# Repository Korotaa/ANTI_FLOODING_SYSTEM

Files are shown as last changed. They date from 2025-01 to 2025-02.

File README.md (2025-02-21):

# Système anti inondation
[https://github.com/Korotaa/ANTI_FLOODING_SYSTEM](https://github.com/Korotaa/ANTI_FLOODING_SYSTEM)
## I. Besoins du système  
1. Détection proactive des niveaux d’eau à l’aide de capteurs robustes.
2. Actionnement automatisé pour évacuation d’eau via une pompe submersible.
3. Signalisation locale et/ou à distance en cas de risque.
4. Résilience énergétique grâce à une batterie de secours.
## II. Design contraintes
1. Fiabilité : Utilisation de capteurs et d’actionneurs éprouvés.
2. Accessibilité : Matériel standard et technologies abordables.
3. Évolutivité : Possibilité d’intégrer des fonctionnalités avancées comme la communication IoT.
##  III. Architecture
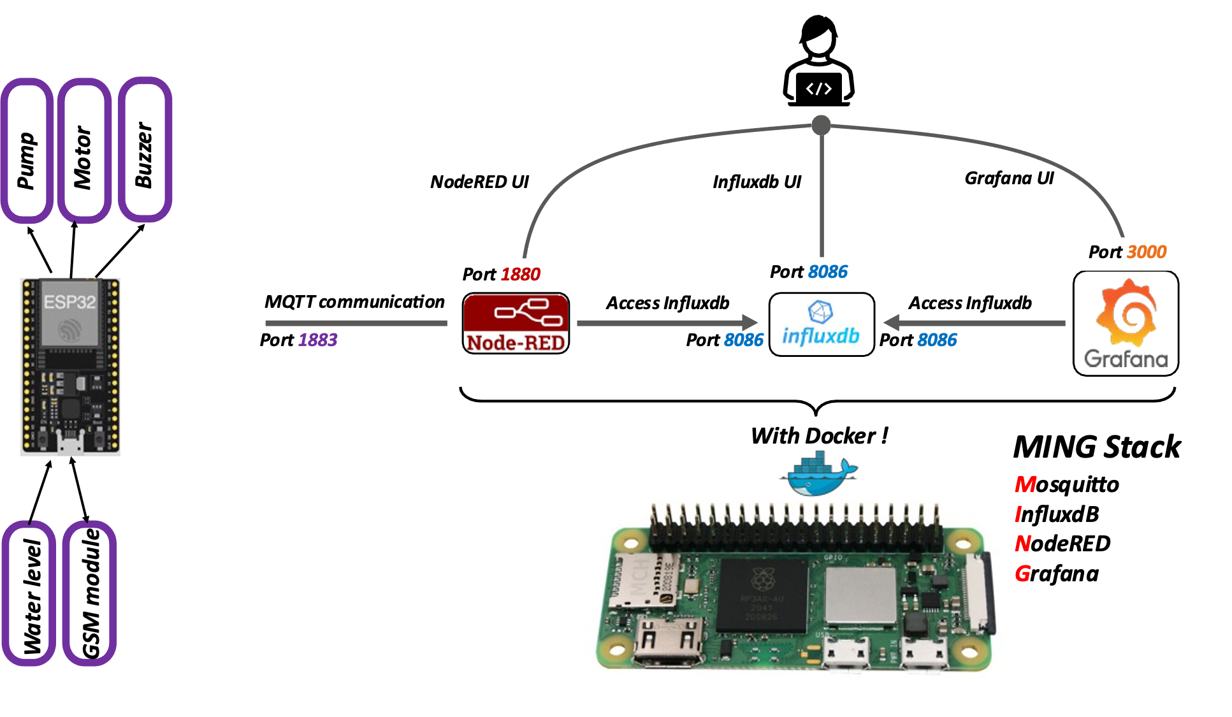
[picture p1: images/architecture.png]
Architecture

## IV. schéma électronique du End-device
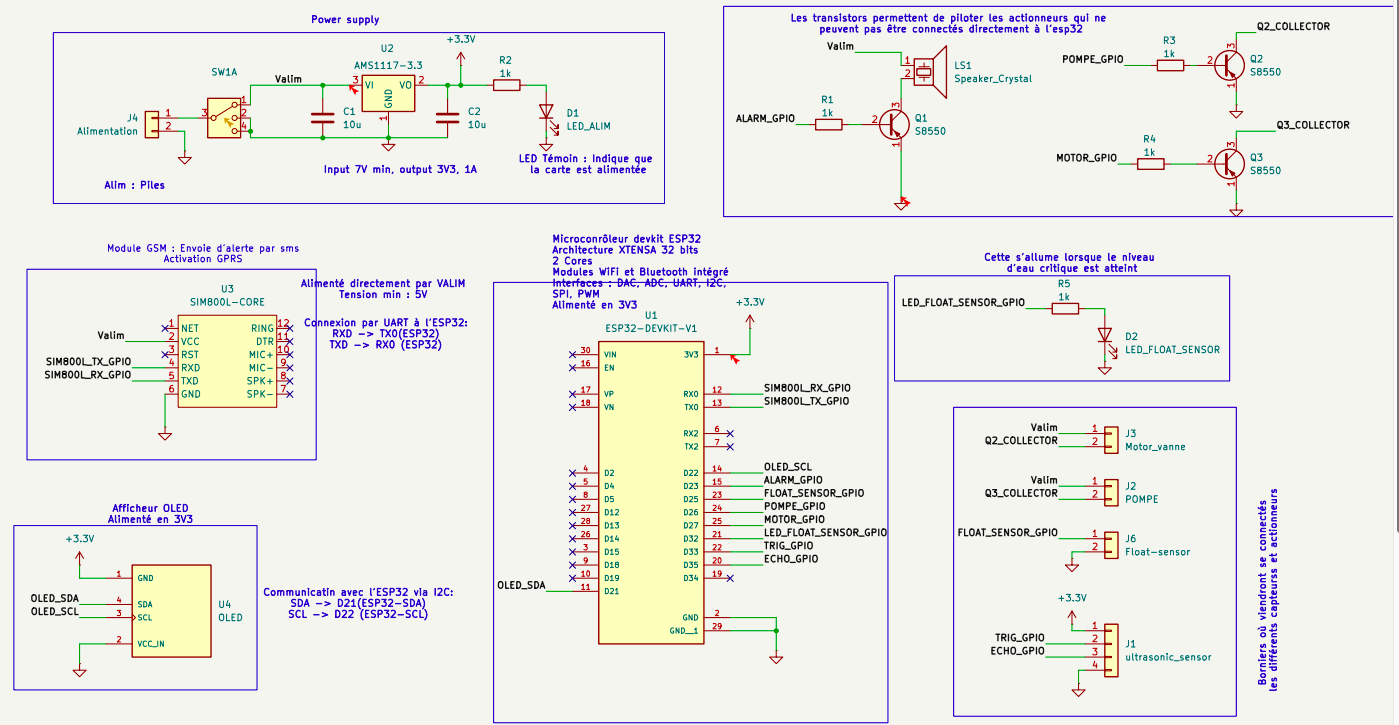
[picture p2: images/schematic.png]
Schematic

## V. PCB
**NB : Le pcb est conçu pour faciliter le prototypage sur PCB double face perforé**
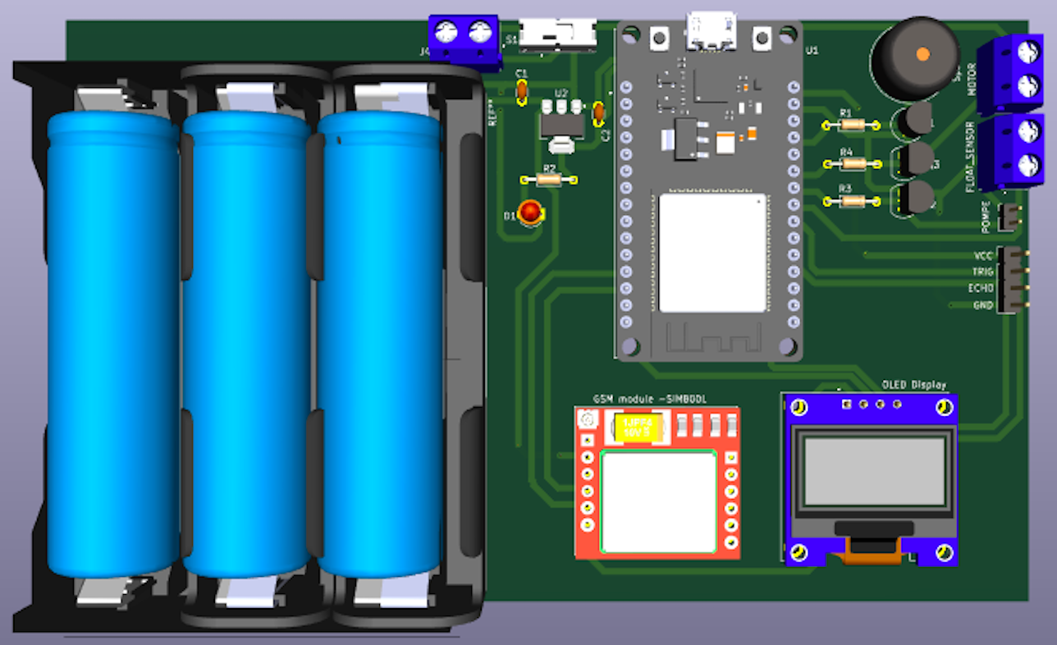
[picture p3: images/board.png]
PCB board


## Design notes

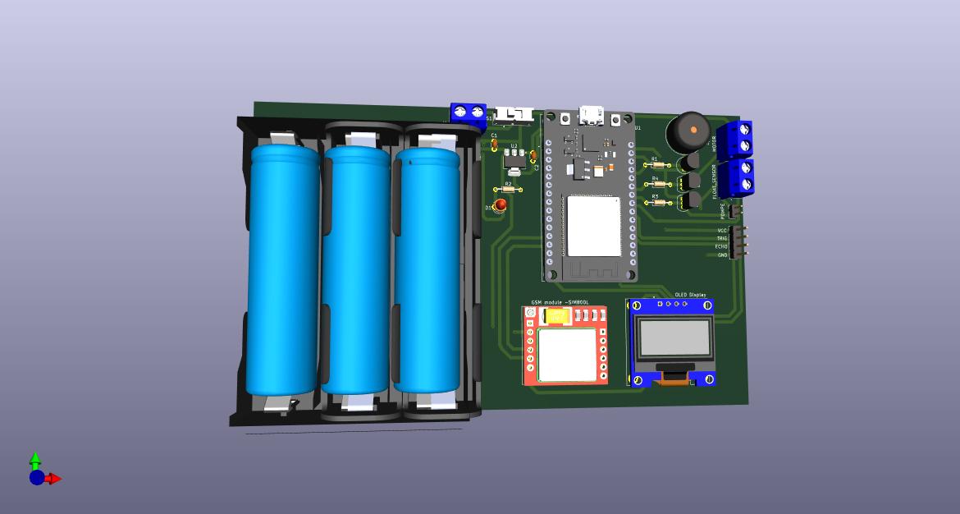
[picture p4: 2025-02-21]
Hardware/anti-innondation-board/Anti_innondation_project1.jpg

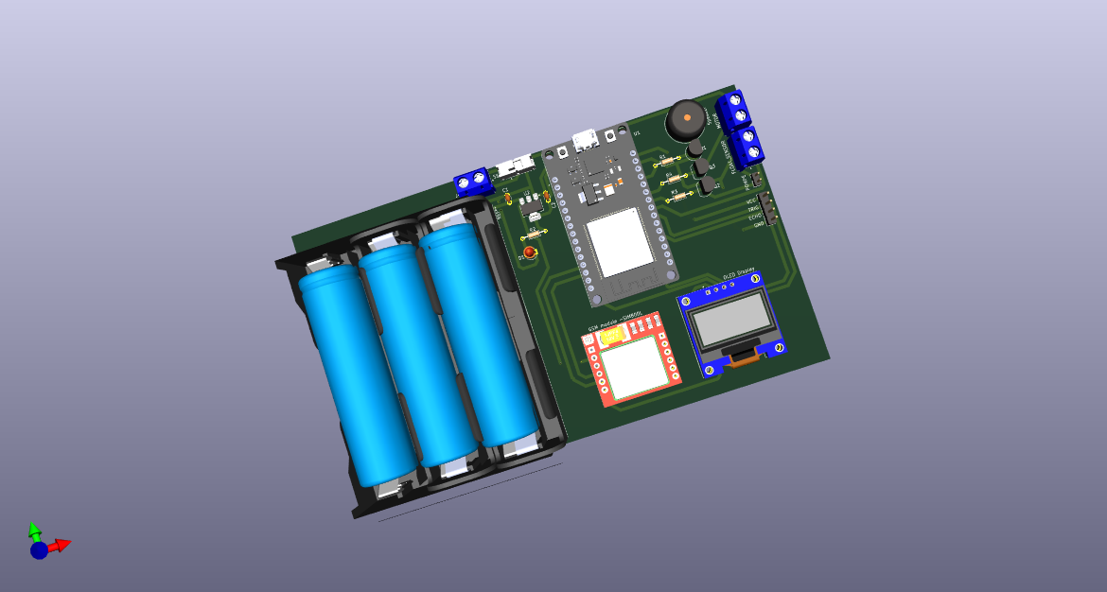
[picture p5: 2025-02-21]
Hardware/anti-innondation-board/pcb_img.png

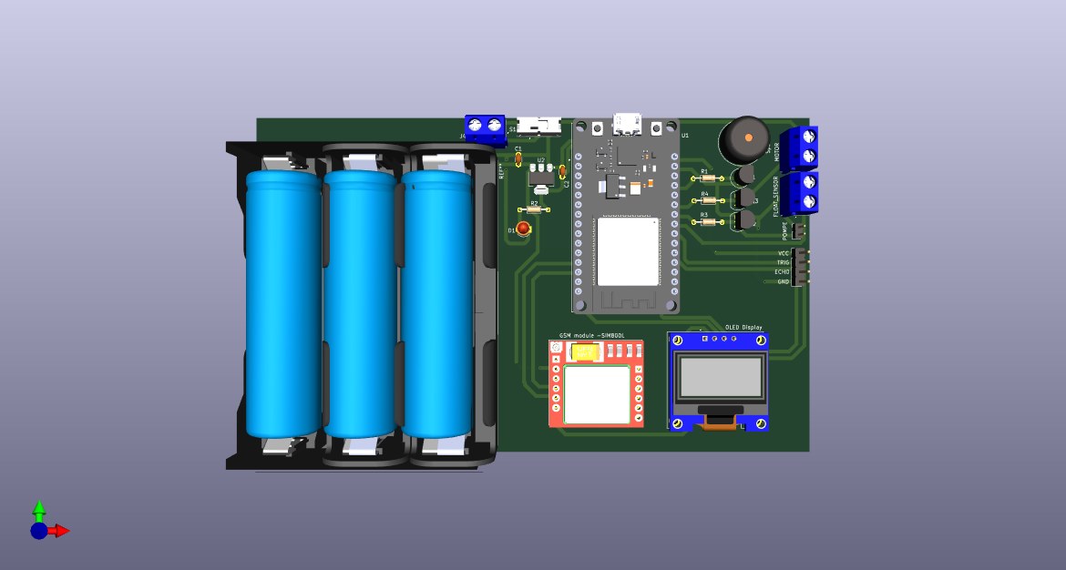
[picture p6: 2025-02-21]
Hardware/anti-innondation-board/anti-innondation-board.png

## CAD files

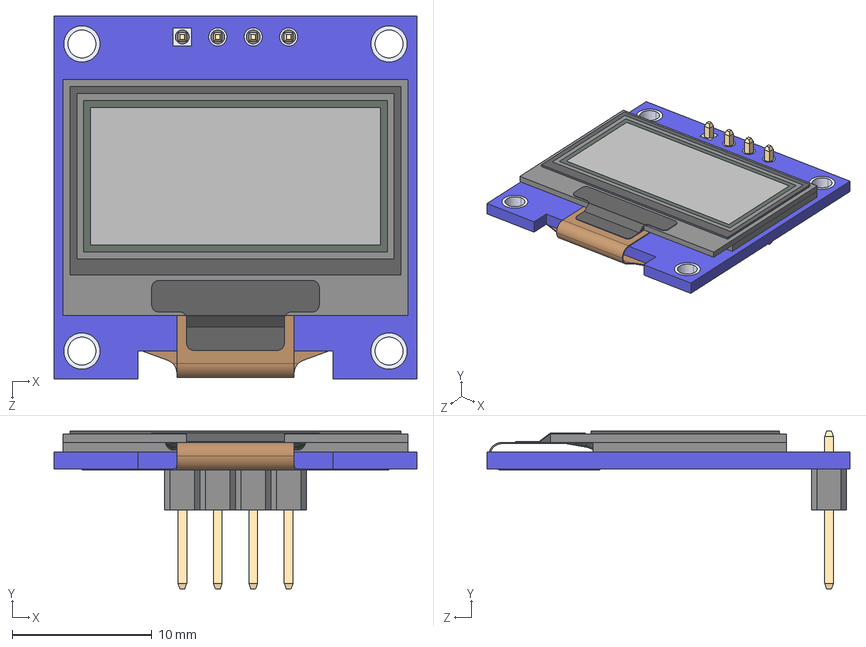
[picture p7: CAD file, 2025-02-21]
Hardware/anti-innondation-board/MY_LIBRARY/1/DM-OLED096-636.step
26.0 x 11.3 x 26.0 mm
DM-OLED096-636_Module
DM-OLED096-636_Panel

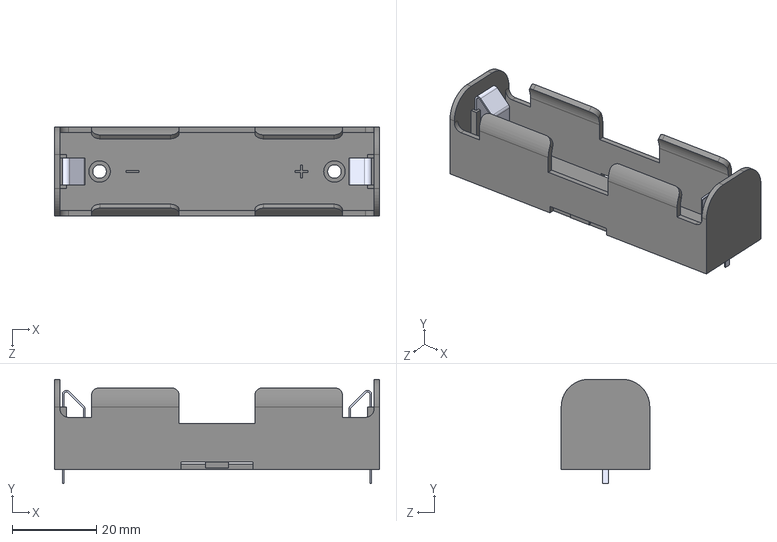
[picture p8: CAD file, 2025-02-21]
Hardware/anti-innondation-board/MY_LIBRARY/BK-18650-PC2--3DModel-STEP-56544.STEP
77.0 x 24.7 x 21.0 mm

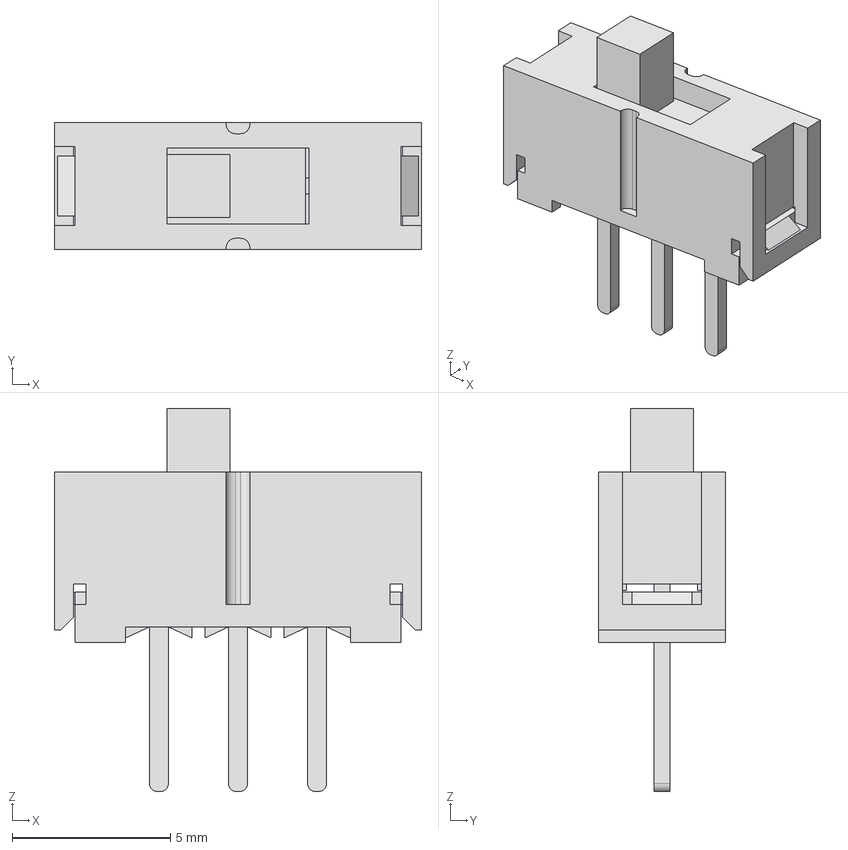
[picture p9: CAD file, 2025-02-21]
Hardware/anti-innondation-board/MY_LIBRARY/EG1218/EG1218.step
11.6 x 4.00 x 12.1 mm

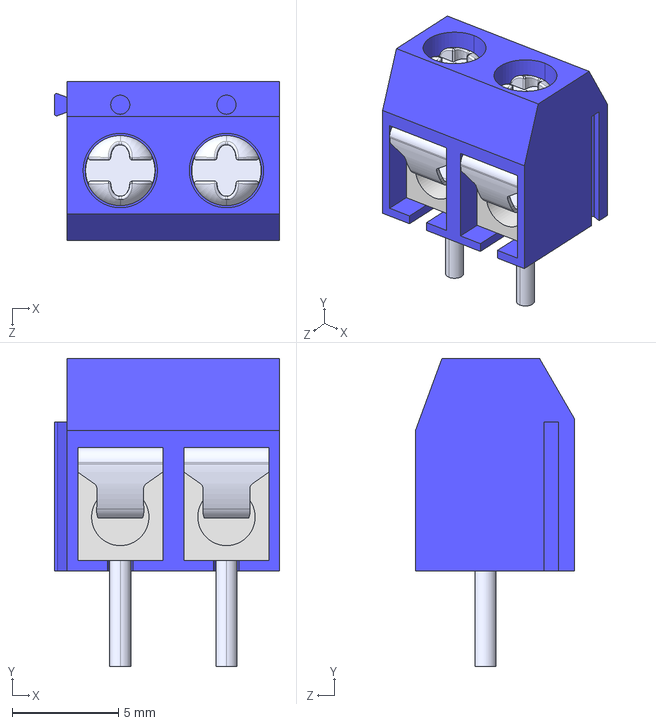
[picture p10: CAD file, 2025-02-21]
Hardware/anti-innondation-board/MY_LIBRARY/KF301-2P/KF301-2P.step
10.6 x 14.5 x 7.50 mm

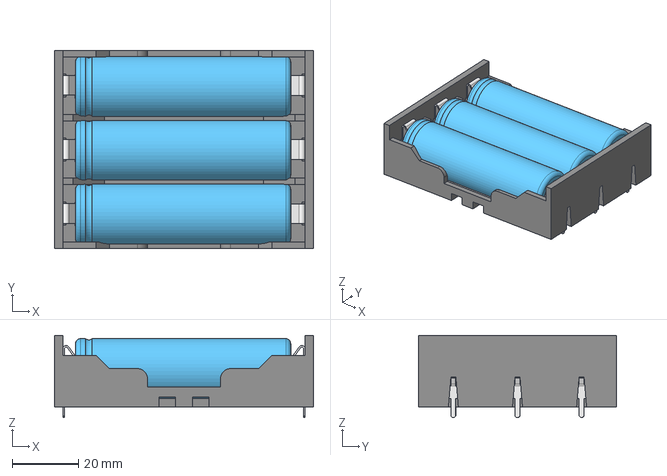
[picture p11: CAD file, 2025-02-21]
Hardware/anti-innondation-board/MY_LIBRARY/3 Battery Holder With Batteries.step
78.0 x 59.6 x 24.7 mm

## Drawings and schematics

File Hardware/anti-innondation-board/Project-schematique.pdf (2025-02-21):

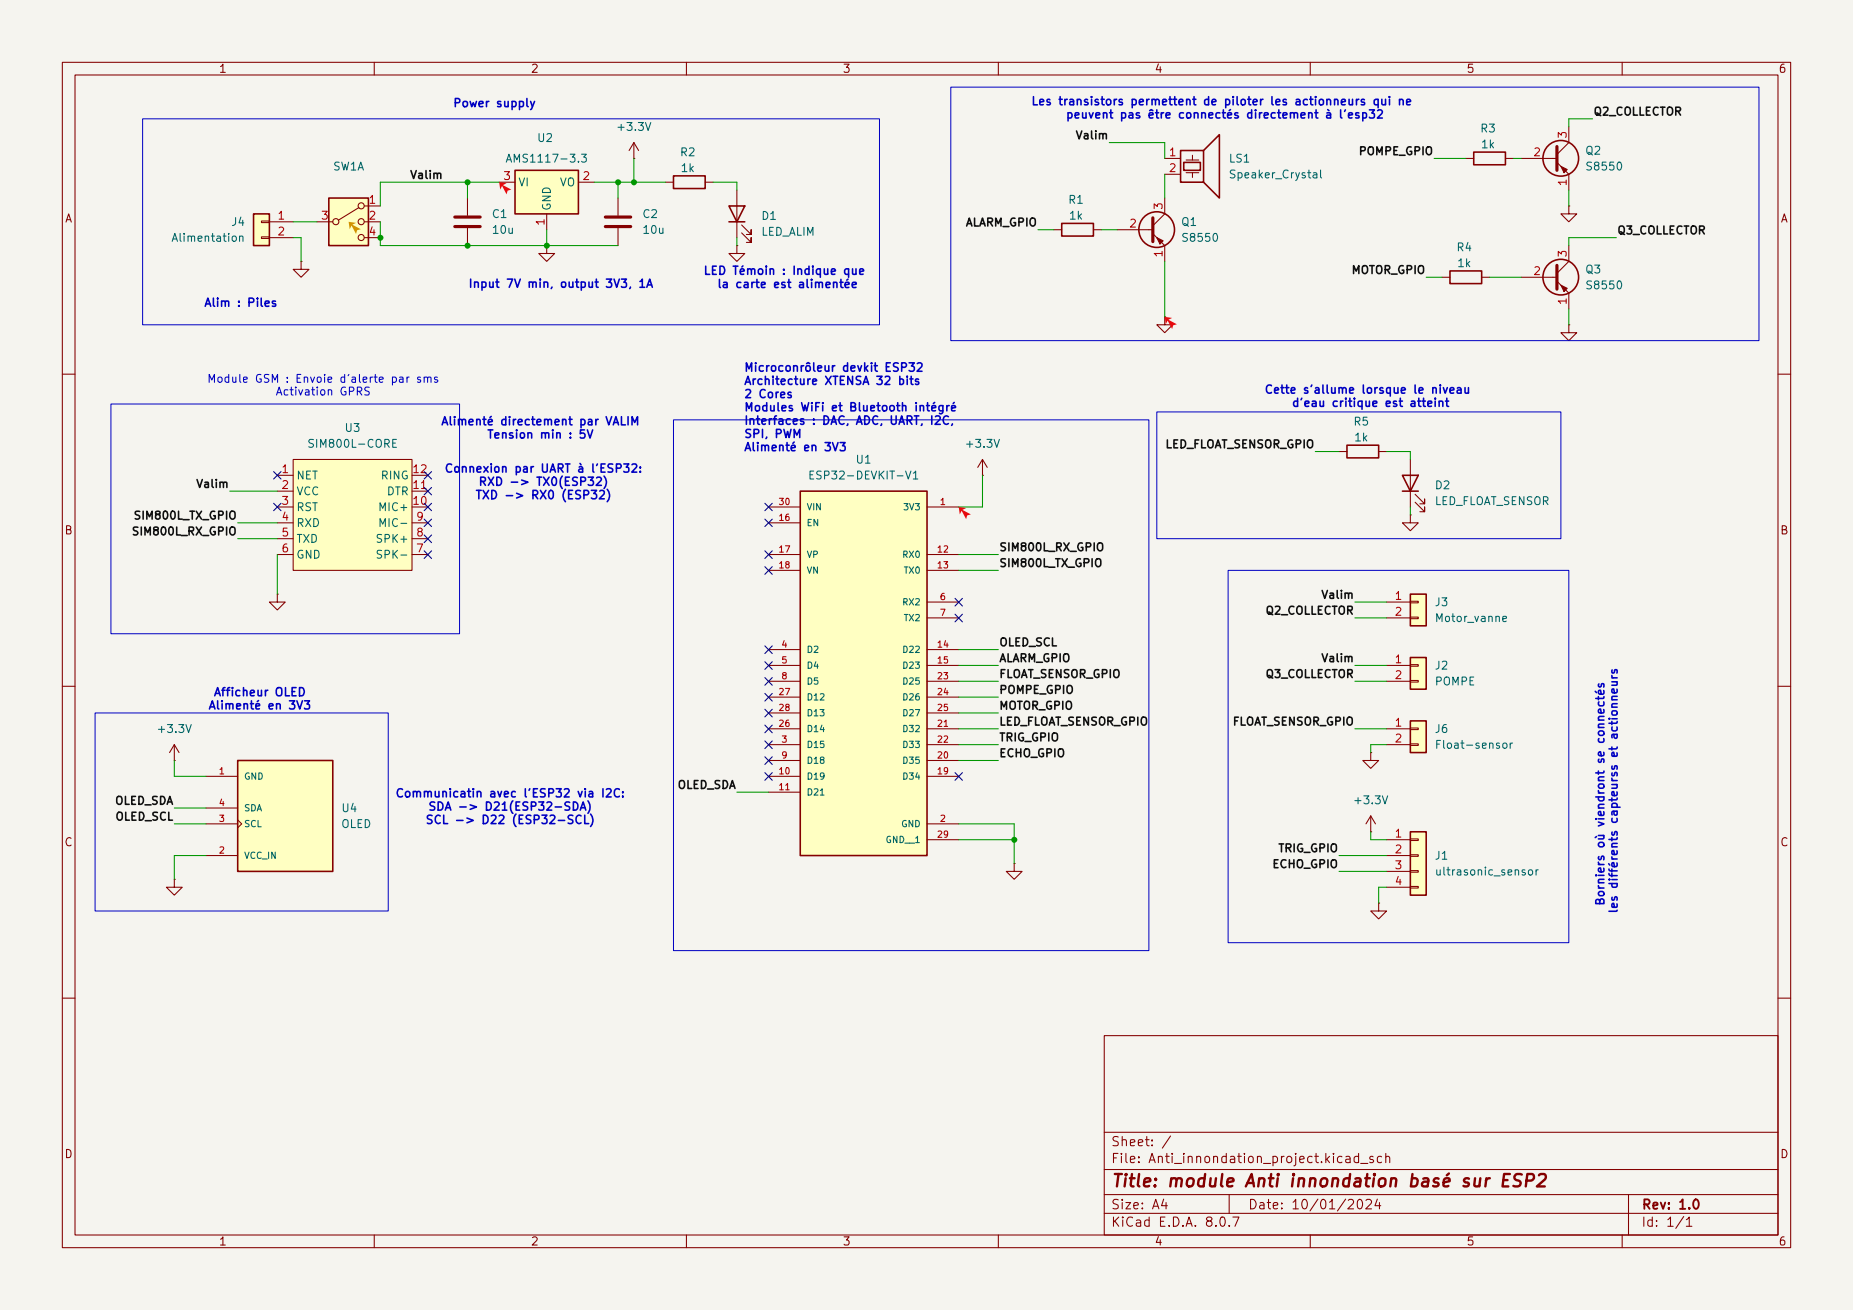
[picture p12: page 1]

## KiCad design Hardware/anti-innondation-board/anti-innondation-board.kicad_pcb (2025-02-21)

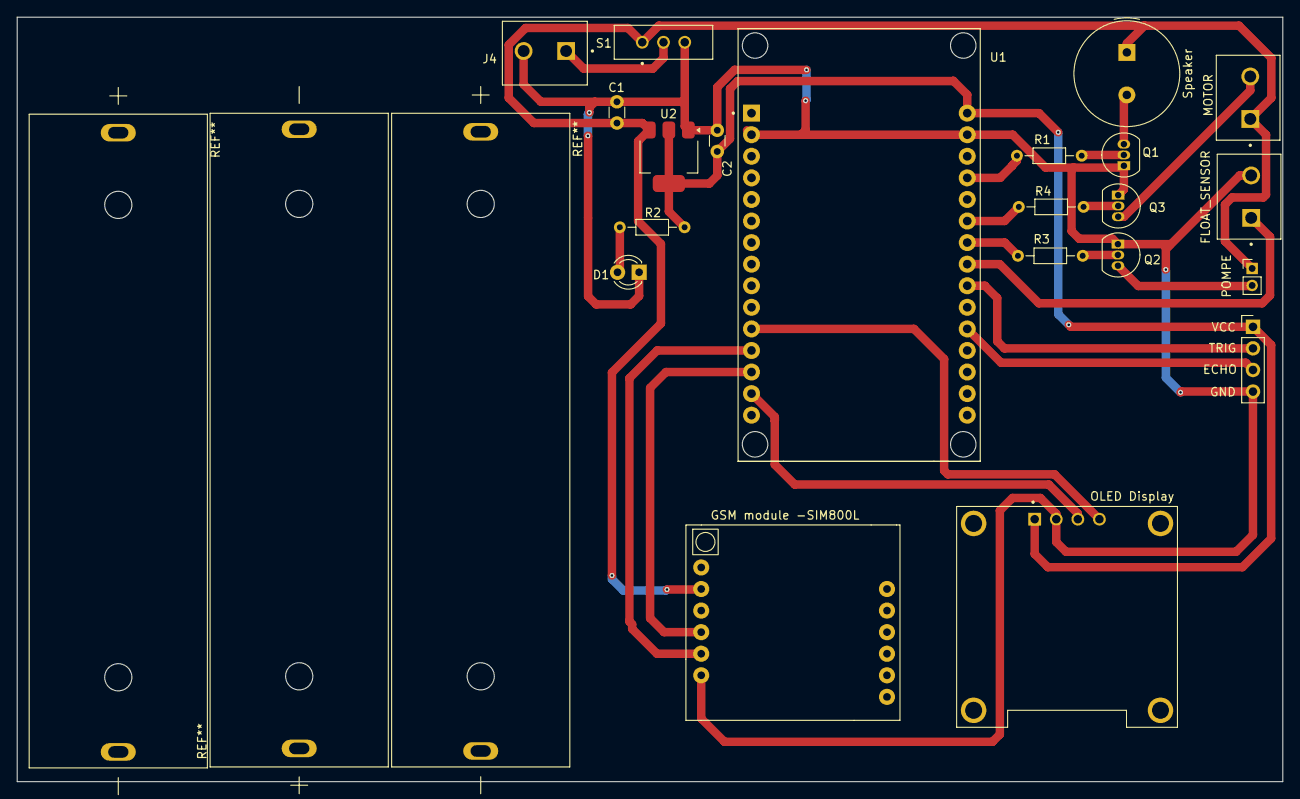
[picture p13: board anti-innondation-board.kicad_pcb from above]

Board: 2 copper layers, 149.0 x 90.0 mm, 21 parts (0 on the bottom side), 21 nets.

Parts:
C1: 22u; C_Disc_D3.0mm_W1.6mm_P2.50mm
C2: 10u; C_Disc_D3.0mm_W1.6mm_P2.50mm
D1: LED_ALIM; LED_D3.0mm
FLOAT_SENSOR: Float-sensor; HANDSON_KF301-2P
GSM module -SIM800L: SIM800L-CORE; SIM800L
J4: Alimentation; HANDSON_KF301-2P
MOTOR: POMPE; HANDSON_KF301-2P
OLED Display: OLED; MODULE_DM-OLED096-636
POMPE: Motor_vanne; PinHeader_1x02_P2.00mm_Vertical
Q1, Q2, Q3: S8550; TO-92_Inline
R1, R2, R3, R4: 1k; R_Axial_DIN0204_L3.6mm_D1.6mm_P7.62mm_Horizontal
S1: EG1218; SW_EG1218
Speaker: Speaker_Crystal; Buzzer_TDK_PS1240P02BT_D12.2mm_H6.5mm
U1: ESP32-DEVKIT-V1; MODULE_ESP32_DEVKIT_V1
U2: AMS1117-3.3; SOT-223-3_TabPin2
VCC: ultrasonic_sensor; PinHeader_1x04_P2.54mm_Vertical

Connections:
+3.3V: C2.1, OLED Display.1 (GND), R2.1, U1.30 (VIN), U2.2 (VO), VCC.1
/ALARM_GPIO: R1.1, U1.27 (D12)
/ECHO_GPIO: U1.20 (D35), VCC.3
/FLOAT_SENSOR_GPIO: FLOAT_SENSOR.1, U1.23 (D25)
/MOTOR_GPIO: R4.1, U1.25 (D27)
/OLED_SCL: OLED Display.3 (SCL), U1.14 (D22)
/OLED_SDA: OLED Display.4 (SDA), U1.11 (D21)
/POMPE_GPIO: R3.1, U1.24 (D26)
/Q2_COLLECTOR: POMPE.2, Q2.3 (C)
/Q3_COLLECTOR: MOTOR.2, Q3.3 (C)
/SIM800L_RX_GPIO: GSM module -SIM800L.5 (TXD), U1.12 (RX0)
/SIM800L_TX_GPIO: GSM module -SIM800L.4 (RXD), U1.13 (TX0)
/TRIG_GPIO: U1.22 (D33), VCC.2
/Valim: C1.1, GSM module -SIM800L.2 (VCC), MOTOR.1, POMPE.1, S1.1, Speaker.1, U2.3 (VI)
GND: C1.2, C2.2, D1.1 (K), FLOAT_SENSOR.2, GSM module -SIM800L.6 (GND), J4.2, OLED Display.2 (VCC_IN), Q1.1 (E), Q2.1 (E), Q3.1 (E), S1.3, U1.2 (GND), U1.29 (GND__1), U2.1 (GND), VCC.4
unnamed: D1.2 (A), R2.2
unnamed: J4.1, S1.2
unnamed: Q1.2 (B), R1.2
unnamed: Q1.3 (C), Speaker.2
unnamed: Q2.2 (B), R3.2
unnamed: Q3.2 (B), R4.2

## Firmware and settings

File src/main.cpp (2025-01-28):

/**
 * @file main.cpp
 * @author your name (you@domain.com)
 * @brief 
 * @version 0.1
 * @date 2025-01-17
 * 
 * @copyright Copyright (c) 2025
 * 
 */
#include <Arduino.h>
#include  <WiFi.h>
#include <ArduinoJson.h>
#include <ArduinoJson.hpp>
#include "ledBlink.h"
#include "config.h"
#include "wificonfig.h"
#include "ultrasonic.h"
#include "configOLED.h"
#include "alarm.h"
#include "floatLevelSensor.h"
#include "pompeControl.h"
#include "configMQTT.h"

int ETAT_POMPE;
int ETAT_ALARM;

void setup() {
  Serial.begin(BAUDERATE);
  pinMode(LED_GPIO, OUTPUT);
  //WiFi connexion
  wifiConnect();
  //MQTT
  setupMQTT();
  initUltrasonic();
  setupOLED();
  pompeInit();
  initAlarm();
  display.setCursor(0, 0);
  display.clearDisplay();
  display.setTextSize(2.75);
  display.println("korota:");
  //display.setTextSize(3);
  //display.println(timeString);
  display.display();
}

void loop() {

  connectToServerMQTT();
  
  StaticJsonDocument<32> doc;
  char data_to_sent[127];
  int criticLevel = waterLevel();
  float waterlevel = readLevel1();

  if(criticLevel) 
  {
    startPompe();
    ETAT_POMPE = 1;
    blinkLed(LED_GPIO);
    onAlarm();
    ETAT_ALARM = 1;
    delay(500);
    }
  else {
    stopPompe();
    ETAT_POMPE = 0;
    offAlarm();
    ETAT_ALARM = 0;
    delay(2000);

  }
  doc["seuil_critique"] = criticLevel;
  doc["Niveau_eau"] = waterlevel;
  doc["Etat_pompe"] = ETAT_POMPE;
  doc["Etat_alarme"] = ETAT_ALARM;
  serializeJson(doc, data_to_sent);
  
  Serial.println("Read");
  Serial.println(data_to_sent);
  sendDataToServerMQTT(data_to_sent);
  delay(5000);
  /*
  //Serial.print("Distance[cm] = ");
  //Serial.println(readLevel1());
  onAlarm();
  delay(1000);
  offAlarm();
  delay(1000);
  */

}

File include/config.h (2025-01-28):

#include <Adafruit_SSD1306.h>


//LED GPIO
#define LED_GPIO 32

//POMPE GPIO
#define POMPE_GPIO 26

//CAPTEUR DE NIVEAU GPIO
#define FLOAT_SENSOR_GPIO 25

//ULTRASONIC SENSOR GPIOS
#define TRIG_GPIO 33
#define ECHO_GPIO 35

//ALARM GPIO 
#define ALARM_GPIO 23

//MOTOR GPIO
#define MOTOR_GPIO 27

//SIM800L GPIO
#define SIM800L_RX_GPIO 1 
#define SIM800L_TX_GPIO 2
//#define TINY_GSM_MODEM_SIM800L

// Configuration de l'écran OLED
#define SCREEN_WIDTH 128
#define SCREEN_HEIGHT 64
#define OLED_ADDR 0x3C
extern Adafruit_SSD1306 display;

//UART COMMUNICATION SPEED
#define BAUDERATE 115200

//WIFI INFO
extern const char  * SSID;
extern const char * PASSWORD;

//MQTT CONFIG
#define RASPBERRYPI_IP "192.168.11.120"
#define BROKERADDRESS RASPBERRYPI_IP
#define PORT 1883
#define SEND_DATA_TOPIC "/sensors/states"
#define DATA_RECEIVED_TOPIC "/mqttServer/commands"
//#define USERNAME root
//#define PASSWORD root

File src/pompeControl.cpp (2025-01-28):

/**
 * @file pompeControl.cpp
 * @author your name (you@domain.com)
 * @paragraph Définis des fonctions permettant de contrôler la pompe. La pompe est commandée
 * via un transistor PNP. Il faut donc un niveau logique LOW appliquée à la base du transistor 
 * pour démarrer la pompe
 * @version 0.1
 * @date 2025-01-17
 * 
 * @copyright Copyright (c) 2025
 * 
 */

#include "Arduino.h"
#include "pompeControl.h"
#include "config.h"

/**
 * @brief Initialise le GPIO de la pompe 
 * @param void
 * @return void
 */
void pompeInit(){
    pinMode(POMPE_GPIO, OUTPUT);
    digitalWrite(POMPE_GPIO, HIGH);
}
/**
 * @brief Cette fonction Demarre la pompe
 * @param void
 * @return void
 */
void startPompe(){
    digitalWrite(POMPE_GPIO, LOW);
    Serial.println("Pompe démarrer");
}
/**
 * @brief Cette fonction arrête la pompe
 * @param void
 * @return void
 */
void stopPompe(){
    digitalWrite(POMPE_GPIO, HIGH);
    Serial.println("Pompe arrêter");
}

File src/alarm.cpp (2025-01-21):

/**
 * @file alarm.cpp
 * @author your name (you@domain.com)
 * @brief Définit deux fonctions qui allume et éteint l'alarme
 * @version 0.1
 * @date 2025-01-19
 * 
 * @copyright Copyright (c) 2025
 * 
 */
#include <Arduino.h>
#include "config.h"
#include "alarm.h"

void initAlarm(){
    pinMode(ALARM_GPIO, OUTPUT);
}
/**
 * @brief Démarre l'alarme
 * @param void
 * @return void
 */
void onAlarm(){
    //pinMode(ALARM_GPIO, OUTPUT);
    //digitalWrite(ALARM_GPIO, LOW);
    // Joue une tonalité simple de 4000 Hz (La4) pendant 1 seconde
    tone(ALARM_GPIO, 2000, 1000);
    digitalWrite(ALARM_GPIO, HIGH);
    delay(1000);
    digitalWrite(ALARM_GPIO, LOW);
    delay(1000); // Pause de 1 seconde
}
/**
 * @brief Arrêter l'alarme
 * @param void
 * @return void
 */
void offAlarm(){
    //pinMode(ALARM_GPIO, OUTPUT);
    //digitalWrite(ALARM_GPIO, HIGH);
    noTone(ALARM_GPIO);
    delay(1000);
}

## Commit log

2025-01-21 Drivers test
2025-02-21 Hardware update
    [3 Battery Holder With Batteries.step, BK-18650-PC2--3DModel-STEP-56544.STEP, BK-18650-PC2.step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]
